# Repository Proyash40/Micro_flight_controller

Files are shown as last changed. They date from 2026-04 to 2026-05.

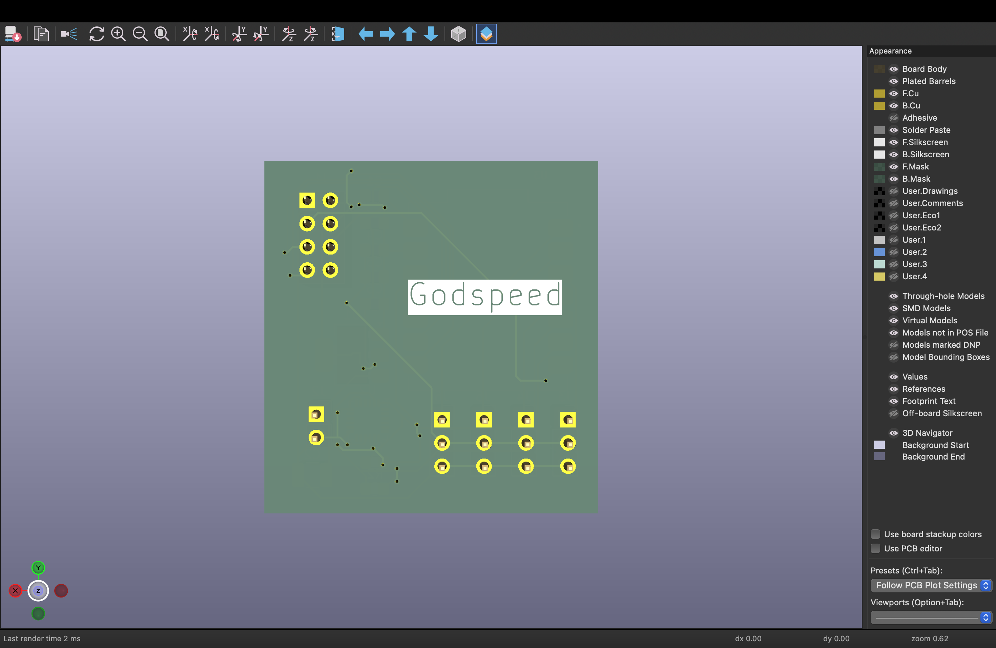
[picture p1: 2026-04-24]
IMAGES/silkscreen2_3d.png

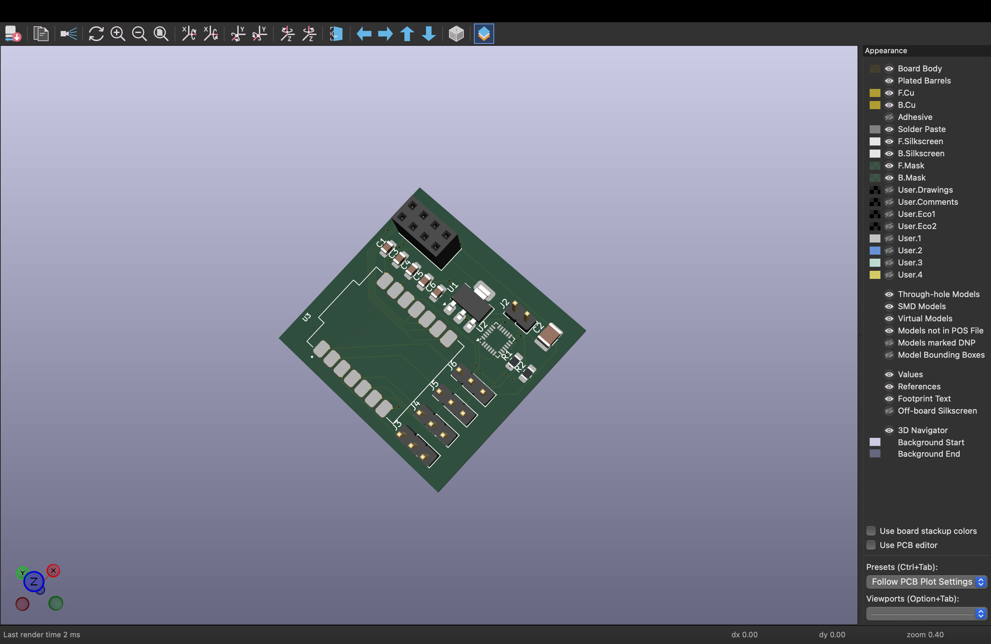
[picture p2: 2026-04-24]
IMAGES/3d_frontview.png

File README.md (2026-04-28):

### Micro flight controller 
Okay so I couldn't find a flight controller small enough or light enough for what I needed, so I just designed one from scratch lol.

It uses a seeed XIAO and a bunch of tiny SMD parts (0805 mostly). it actually works and flies pretty smooth but u have to be okay with soldering things the size of a grain of rice.

---

### What is this?

Basically a 4 channel RC flight computer. it takes throttle, aileron, elevator, and rudder from an nRF24 radio, runs it through some PID math at 100Hz, checks the gyro, and moves the servos so your plane doesn't instantly do a death flip.

### Stuff u need to build this (BOM)
---

| Name | Purpose | Quantity | Price (1 Unit) | Price Total(USD) | Links| 
| :-- | :-- | :-- | :-- | :-- | :-- |
| 4.7k smd resistor| I2C Pull-up for MPU6050  | 2 | $3.61 | $3.61 | [Link](https://robu.in/product/pro-range-resistor-assortment-kit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)|
| AMS1117 | Power Stability | 1 | $0.1 | $0.1 | [link](https://robu.in/product/ams1117-5-0-kexin-800ma-fixed-5v-positive-electrode-18v-sot-223-4-voltage-regulators-linear-low-drop-out-ldo-regulators-rohs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) |
| MPU6050 | 3 axis gyro + accelerometer | 1 | $2.55 | $2.55 | [link](https://quartzcomponents.com/products/mpu-6050-3-axis-gyro-accelerometer-ic-tdk-invensense-qfn-24-smd-package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) |
| Seeed studio XIAO ESP32 supermini C3 | The main brain | 1 | $9.56 | $9.56 | [Link](https://robu.in/product/seeed-studio-xiao-esp32s3-2-4ghz-wifi-ble-5-0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) |
| PCB print | Holding all the components together | 1 | $ 3 | $3 | [Link](https://cart.jlcpcb.com/quote)
| Capacitor 0.1uF (100nF) 0805| Decoupling for MPU6050 | 3 | -- | -- | I'd recomend buying it offline |
| Capacitor 2.2nF 0805 | MPU6050 Charge Pump | 1 |  -- | -- | I'd recomend buying it offline |
| Capacitor 10uF 0805 | AMS1117 Input Filter| 2 |  -- | -- | I'd recomend buying it offline |
| Capacitor 100uF 1210 | nRF24 Power Buffer* | 2 | -- | -- | I'd recomend buying it offline |

### IMPORTANT RANT ABOUT SOLDER

Do NOT use cheap 60/40 or 35/65 solder for this. The vibrations from the drone motors will crack your joints. buy actual 63/37 (Tin/Lead) Rosin Core 0.5mm wire. It solidifies instantly and doesn't get mushy. Soldron is fine. Just don't buy the cheap unbranded tubes.

### Software stuff

The code is in C++. don't use the normal arduino IDE for this, it sucks for complex stuff. Use VS Code + PlatformIO.

### Libraries u need:

RF24 (for the radio)

MPU6050_light (so much better than writing custom kalman filters)

PID_v1 (for the stabilization math)

---

Note: The loop is locked at 100Hz so the servos don't twitch themselves to death. The I2C is boosted to 400kHz so the gyro reads fast enough.

---

### How to fly 

1) Turn on radio.

2) Plug in battery.

3) DO NOT touch the plane for like 3 seconds while the MPU6050 calibrates.

4) Arm the throttle (push it up past 1050us).

5) Pray your PID tuning is right.

---

### Images

rough_idea

Screenshot 2026-04-28 at 12 12 12 PM

schematic

schematic1

pcb

silkscreen1

3d_frontview

silkscreen2_3d

---
If u haven't flown any rc before, I'd recomend to let someone experienced fly it first unless you want to destroy all your hard work on  the first flight.

---
(Disclaimer: if u copy my PID values and your plane nosedives into a tree, that's on u. tune it yourself for your airframe).

Have fun ✌️

### ~GODSPEED

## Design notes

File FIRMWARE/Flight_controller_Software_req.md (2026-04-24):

Flight Controller - Firmware Dependencies

## Development Environment
* **IDE:** VS Code with the PlatformIO extension (Highly recommended over the basic Arduino IDE for a project this complex).
* **Framework:** Arduino Core
* **Board Manager URL/Package:** * `Earle Philhower's arduino-pico` (If using the XIAO RP2040)
  * `Seeed nRF52 mbed-enabled Boards` (If using the XIAO nRF52840)

## Core Libraries (Install via Library Manager)

### 1. Radio Communication
* **Library:** `RF24` 
* **Author:** TMRh20
* **Purpose:** The absolute gold standard for driving the nRF24L01. It handles the SPI communication, packet payloads, and error checking.

### 2. Sensor Fusion (MPU6050)
* **Library:** `MPU6050_Light` 
* **Author:** Romain Fétick (rfetick)
* **Purpose:** This is the secret weapon for DIY drones. Instead of reading raw, noisy accelerometer data and writing your own Kalman filters, this library automatically calculates the clean Pitch, Roll, and Yaw angles fast enough for a flight controller. 

### 3. Flight Stabilization (The Math)
* **Library:** `PID_v1`
* **Author:** Brett Beauregard
* **Purpose:** You need a PID (Proportional, Integral, Derivative) loop for Pitch, Roll, and Yaw to keep the plane level. This library handles the complex calculus for you. You just feed it your current angle and your desired angle, and it outputs the correction needed.

### 4. Hardware Outputs
* **Library:** `Servo` (Built-in)
* **Purpose:** Generates the exact 50Hz PWM signals required to talk to the ESC (Throttle) and the 3 Servos (Aileron, Elevator, Rudder).

## The Core Software Architecture (The Loop)
Your `void loop()` must run as fast as possible (target >100Hz) in this exact order:
1. **Radio Rx:** Check if a new command packet arrived from the transmitter.
2. **Read IMU:** Get the current pitch/roll angle from the MPU6050.
3. **Compute PID:** Compare the pilot's command to the current angle and calculate the difference.
4. **Mixer:** Mix the PID outputs to figure out exactly how far to move each servo.
5. **Output:** `Servo.write()` the new values to the physical pins.

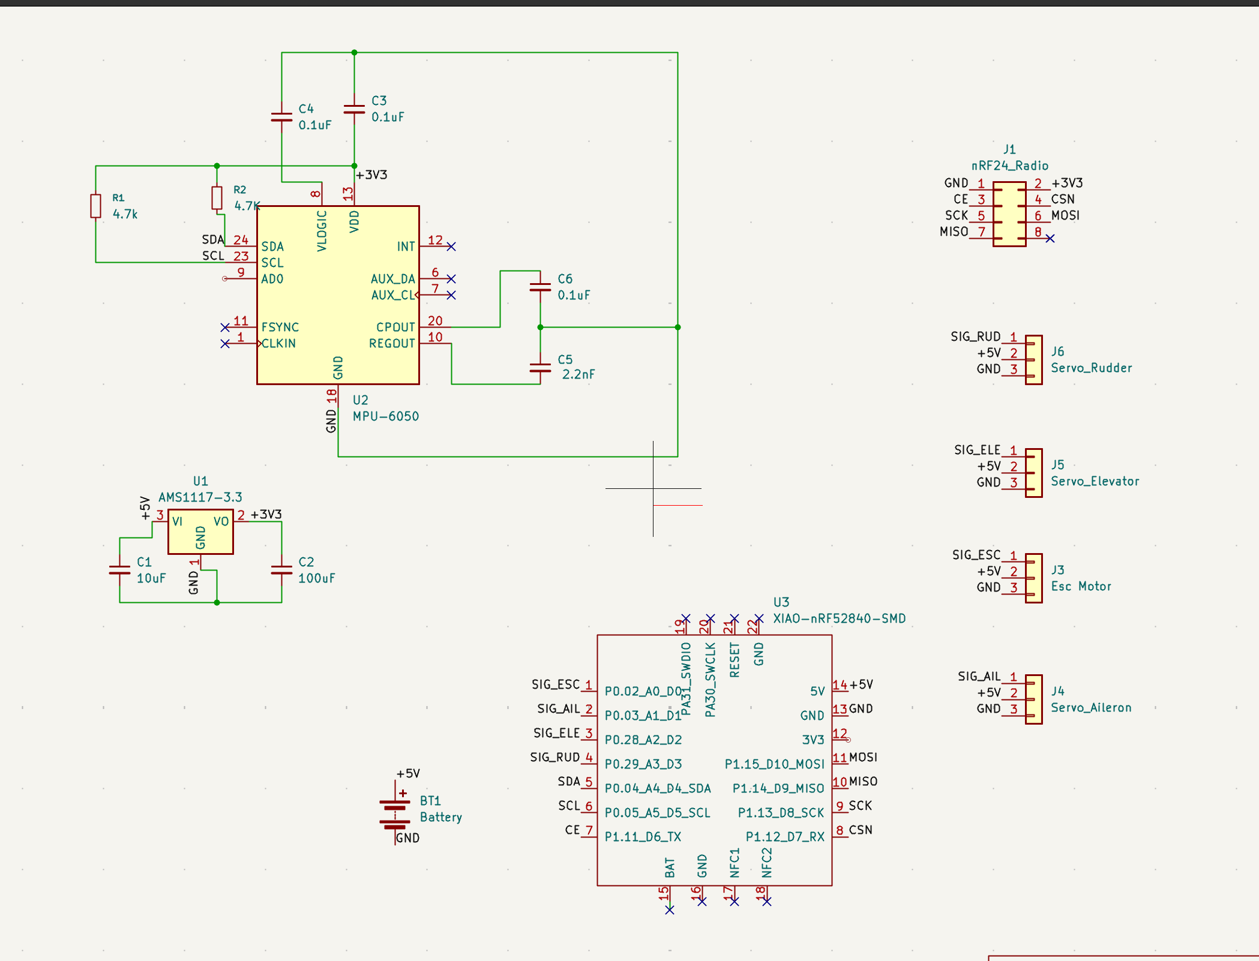
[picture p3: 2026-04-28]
IMAGES/schematic.png

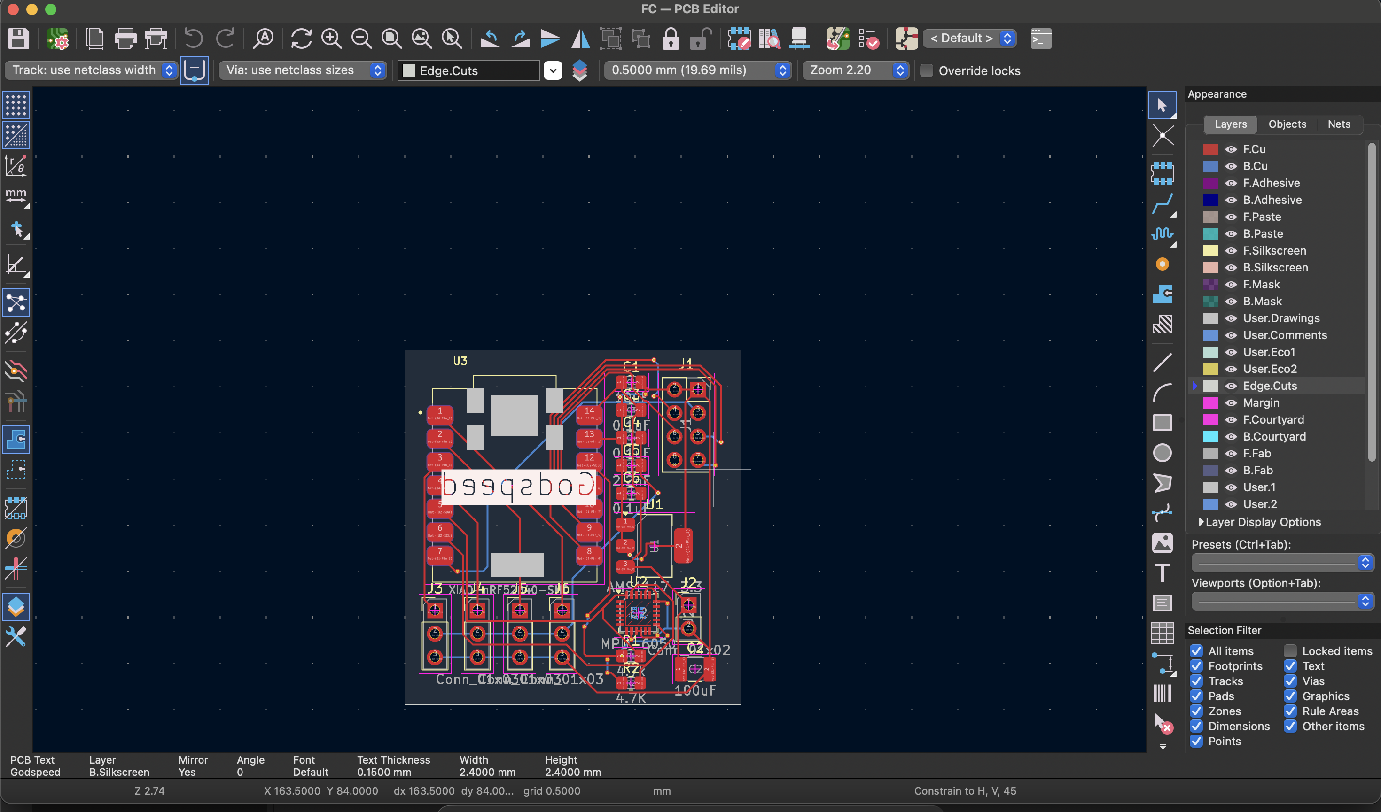
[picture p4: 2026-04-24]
IMAGES/silkscreen1.png

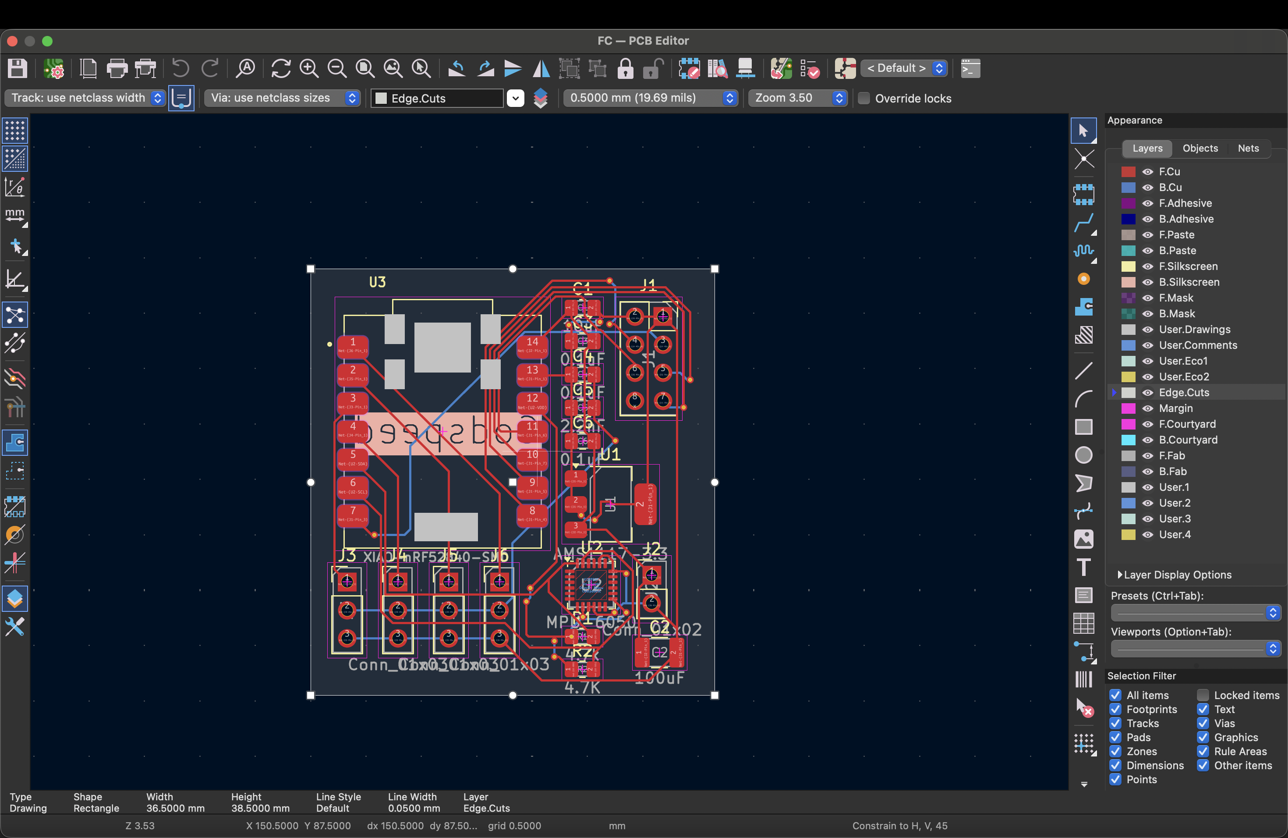
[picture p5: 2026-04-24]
IMAGES/pcb.png

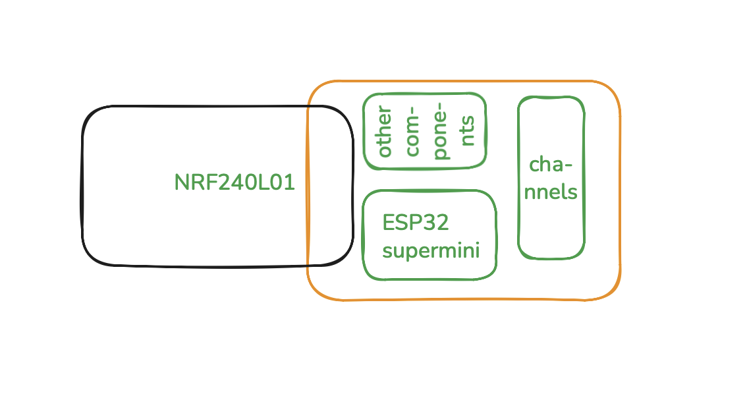
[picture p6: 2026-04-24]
IMAGES/rough_idea.png

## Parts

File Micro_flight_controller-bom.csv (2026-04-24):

Name | Purpose | Quantity | Total Cost (USD) | Link | Distributor
4.7k resistance | I2C Pull-ups for MPU6050 | 1 | 3.61 | https://robu.in/product/pro-range-resistor-assortment-kit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 | Robu.in
AMS1117 | power stability | 1 | 0.10 | https://robu.in/product/ams1117-5-0-kexin-800ma-fixed-5v-positive-electrode-18v-sot-223-4-voltage-regulators-linear-low-drop-out-ldo-regulators-rohs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 | Robu.in
MPU6050 | 3 axis Gyro+ accelerometer | 1 | 2.55 | https://quartzcomponents.com/products/mpu-6050-3-axis-gyro-accelerometer-ic-tdk-invensense-qfn-24-smd-package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 | Quartz components
Seeed studio ESP32 | The main brain | 1 | 9.56 | https://robu.in/product/seeed-studio-xiao-esp32s3-2-4ghz-wifi-ble-5-0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 | Robu.in

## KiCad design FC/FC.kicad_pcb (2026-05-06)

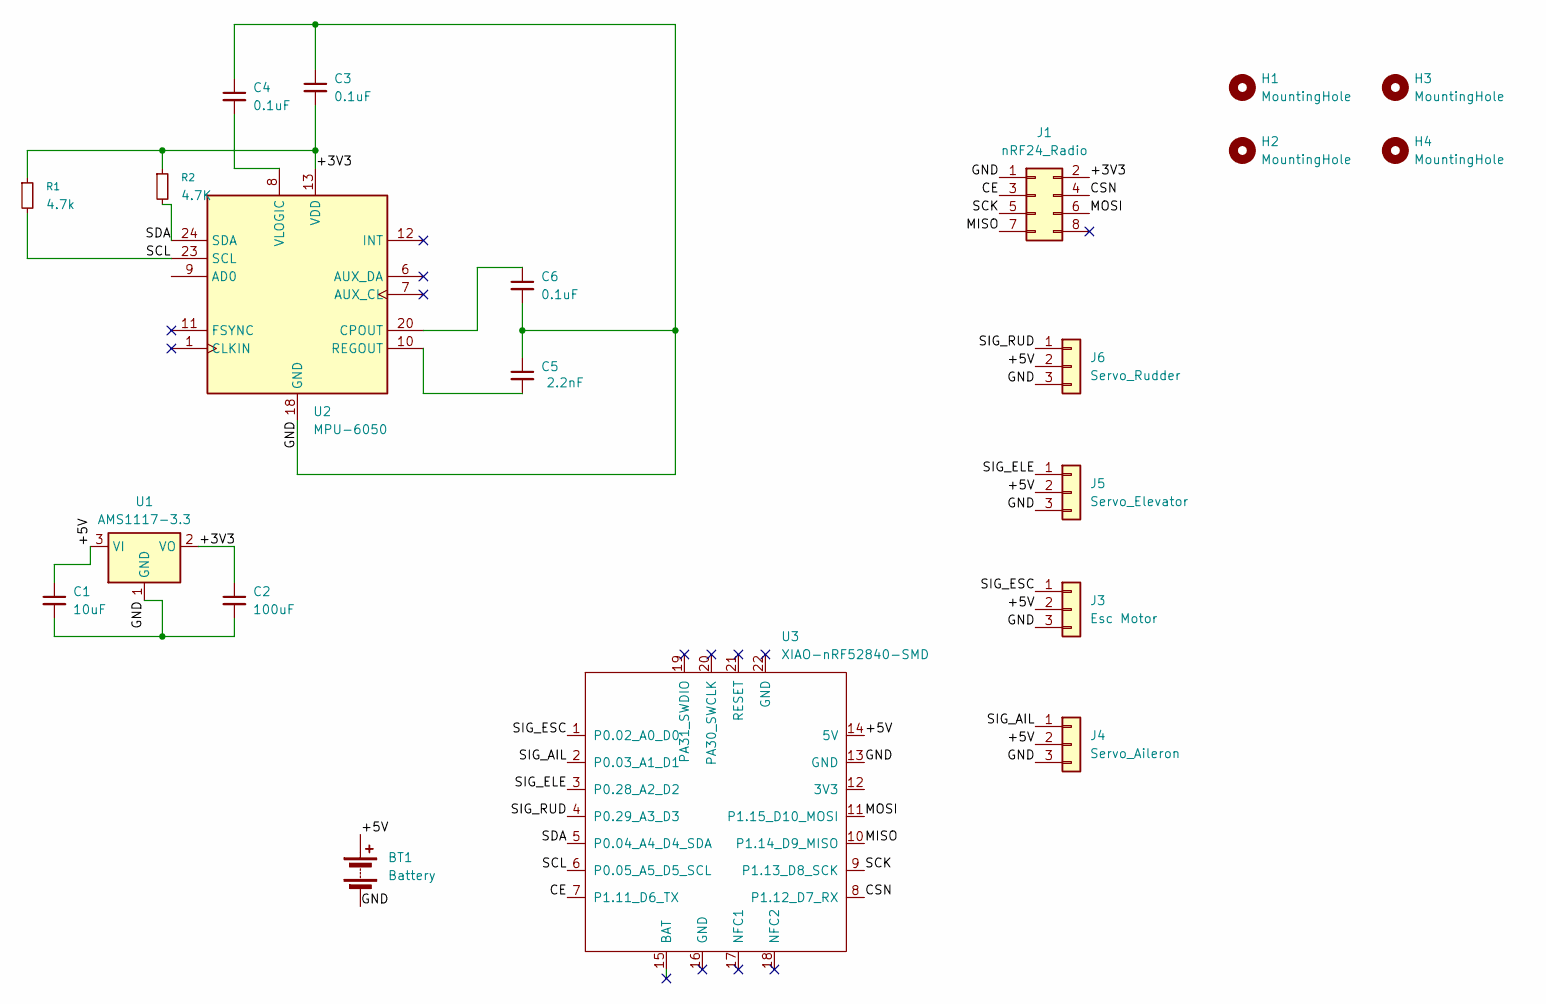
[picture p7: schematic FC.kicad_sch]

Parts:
BT1: Battery; MountingHole_2.2mm_M2
C1: 10uF; C_0805_2012Metric_Pad1.18x1.45mm_HandSolder
C2: 100uF; C_1210_3225Metric_Pad1.33x2.70mm_HandSolder
C3, C4, C6: 0.1uF; C_0805_2012Metric_Pad1.18x1.45mm_HandSolder
C5: 2.2nF; C_0805_2012Metric_Pad1.18x1.45mm_HandSolder
H1, H2, H3, H4: MountingHole; MountingHole_2.2mm_M2
J1: nRF24_Radio; PinSocket_2x04_P2.54mm_Vertical
J3: Esc Motor; PinHeader_1x03_P2.54mm_Vertical
J4: Servo_Aileron; PinHeader_1x03_P2.54mm_Vertical
J5: Servo_Elevator; PinHeader_1x03_P2.54mm_Vertical
J6: Servo_Rudder; PinHeader_1x03_P2.54mm_Vertical
R1: 4.7k; R_0805_2012Metric_Pad1.20x1.40mm_HandSolder
R2: 4.7K; R_0805_2012Metric_Pad1.20x1.40mm_HandSolder
U1: AMS1117-3.3; SOT-223-3_TabPin2
U2: MPU-6050; InvenSense_QFN-24_4x4mm_P0.5mm
U3: XIAO-nRF52840-SMD; MODULE_102010428

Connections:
/+3V3: C2.1, C3.2, J1.2, R1.1, R2.1, U1.2 (VO), U2.13 (VDD)
/+5V: BT1.1 (+), C1.1, J3.2, J4.2, J5.2, J6.2, U1.3 (VI), U3.14 (5V)
/<NO NET>: J5.1, U3.3 (P0.28_A2_D2)
/CE: J1.3, U3.7 (P1.11_D6_TX)
/CSN: J1.4, U3.8 (P1.12_D7_RX)
/GND: BT1.2 (-), C1.2, C2.2, C3.1, C4.1, C5.1, C6.2, J1.1, J3.3, J4.3, J5.3, J6.3, U1.1 (GND), U2.18 (GND), U3.13 (GND)
/MISO: J1.7, U3.10 (P1.14_D9_MISO)
/MOSI: J1.6, U3.11 (P1.15_D10_MOSI)
/SCK: J1.5, U3.9 (P1.13_D8_SCK)
/SCL: R1.2, U2.23 (SCL), U3.6 (P0.05_A5_D5_SCL)
/SDA: R2.2, U2.24 (SDA), U3.5 (P0.04_A4_D4_SDA)
/SIG_AIL: J4.1, U3.2 (P0.03_A1_D1)
/SIG_ESC: J3.1, U3.1 (P0.02_A0_D0)
/SIG_RUD: J6.1, U3.4 (P0.29_A3_D3)
unnamed: C6.1, U2.20 (CPOUT)
unnamed: C5.2, U2.10 (REGOUT)
unnamed: C4.2, U2.8 (VLOGIC)

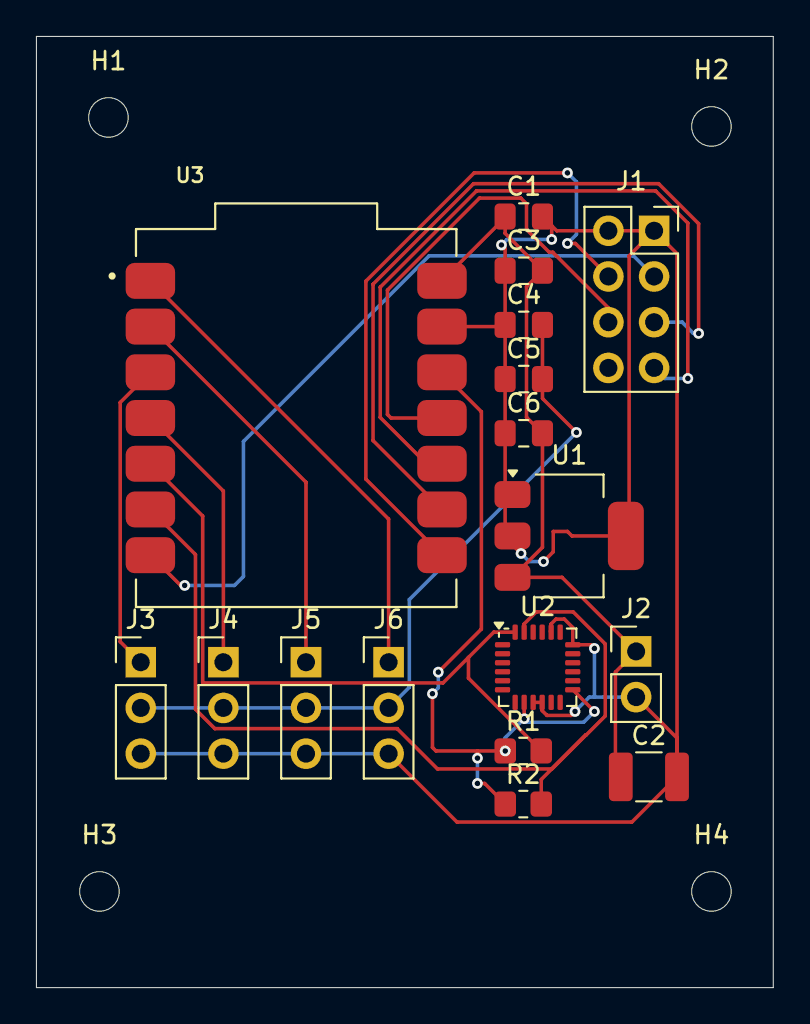
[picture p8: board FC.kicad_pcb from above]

Board: 2 copper layers, 40.9 x 52.8 mm, 21 parts (0 on the bottom side), 17 nets.

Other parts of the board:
J2: Conn_01x02; PinHeader_1x02_P2.54mm_Vertical

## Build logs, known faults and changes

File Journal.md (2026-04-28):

### Journal :-

| Title | Micro Flight Controller |
| :-- | :---|
|Author | Proyash Kumar Sarkar (Godspeed)|
|Project Tire | 3|

### Components searching, basic design

This was my first time designing a cutom flight controller. Prior to this i had flown rc planes nd had experience with transmitter nd receiver making, so with a certain motivation by my frnd, i started working on this project.

At the begining i had to know about the componets of the flight controller, the sensors or function it does, then chose the right material and the smaller the better. We all know how hard its to make rc plane fly with heavy components.

So the first challenge was to find the componets small enough and fits the budget. First i was seacrhing for [ELRS](https://robu.in/product/radiomaster-tx16s-mkii-hall-v4-0-elrs-radio-controller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) modules then saw the price nd nearly pulled my heart out. So i went with the standard NRF240L01+(PA+LNA) module, it gives a range for about 700-1km, which is fairly good enough for a beginner project. {Cutting cost does comes with some drawbacks🥲}

Howsoever, after that, chossing the main brain, yea it was hecktic. Cz I myself prefer design PCB with KiCAD, now it doesn't have the footprint nor the library nor the symbol for Seeed studio Xiao ESP32 supermini. So i was thinking what the brain i might use. I called one of my friend nd he advised me to see this [video](https://www.youtube.com/watch?v=W9cLnIjvybo) by [PlumPot](https://www.youtube.com/@PlumPot). Then learnt how to insert or import whatever, to KiCAD and use it, so i went with the ESP32. (I used nothing else due to its tiny size and processing speed)

At the end i chose the MPU6050 module, it has 3 axis gyro and additionally accelerometer.

So finnally this was the basic design. I just tried to make the Flight Controller as small as possible.

---

rough_idea

---

Now lets see, how small I can make the PCB✌🏻

---
### The circuit design

Screenshot 2026-04-28 at 12 12 12 PM

This was my circuit diagram, I know its very hard to understand, so I'd recommned to look at the schematic which I'd make later on. And also I've not checked the whole diagram precisely, there is some issues with it which i ddecided to fix in the schematic.

---

### Schematic and PCB design

This morning, as soon as i woke up started gathering stuffs in KiCAD. But as i had mentioned in my last journal, it was pretty difficult to find the parts by their names. So I took some help for gemini and also google(not gonna lie😅)

So, after i found all the componenets and their libraries, i started making the schematic. For god's sake, it was very very difficult, i spent most of the time thinking, where to connect, nd with so many components. 😭

Though after a lot of struggle i managed to complete the schematic. Plot twist, as soon as I ran ERC, it gave a bunch of errors and warnings. It was my time to start crying. I slammed my laptop off, and went to bed with spotify at the full volume of my music system. Nd my mom came with her slippers in hand.😂

So I put on my headphones nd slept. after about an hour or so I woke up did some Maths for upcoming exams.(Yea ive not included this time in the session time). Then with a fresh mind i started making the schematic again and boom, i succesfully made the schematic.

---
schematic

---
schematic1

I later cleanedup the schematic for a better understanding. And note that I've forgotten to add the "no connection mark" on the ESP32 3V3 pin, it wont create any blunder but while running ERC, it might show as unconnected port, thats all.

:) 
---

Then assigned the footprints, I downloaded the footprint for this specific ESP32 from [here](https://www.snapeda.com/parts/102010428/Seeed%20Technology%20Co.%2C%20Ltd/view-part/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) and added to my library. Though it was pretty easy, but i forgot to save the footprint at first, nd was really screaming when i switched to PCB mode, as i couldn't see any of the components. Then i again went back and saved the footprints. Joined the wires again and prepared my mini PCB which is almost as small as a 4*4 cm square.

---

pcb

---

### Searching on Web for availability of the components

So finally after web screapping a lot, i found the materials i required and additonally keeping in mind the budget. So these given below are my whole listt of components. Hopefully they work all fine nd i myself don't make any mistake😅

---
robu_bill

quartz_components_bill

jlc_pcb_bill

---

### Project under [Stasis](https://stasis.hackclub.com/dashboard/projects/cmobnjizc019h01mn31wxweli)

### ~GODSPEED

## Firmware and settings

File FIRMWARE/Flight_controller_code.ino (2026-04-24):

#include <Wire.h>
#include <Servo.h>
#include <RF24.h>
#include <MPU6050_light.h>
#include <PID_v1.h>

RF24 radio(6, 7);
const byte address[6] = "00001";

MPU6050 mpu(Wire);

Servo esc;
Servo aileron;
Servo elevator;
Servo rudder;

struct RadioPacket {
  int throttle;
  int pitch;
  int roll;
  int yaw;
  bool arm;
};

RadioPacket data;

double pitchInput, pitchOutput, pitchSetpoint;
double rollInput, rollOutput, rollSetpoint;

double kp = 2.0, ki = 0.5, kd = 1.0;

PID pitchPID(&pitchInput, &pitchOutput, &pitchSetpoint, kp, ki, kd, DIRECT);
PID rollPID(&rollInput, &rollOutput, &rollSetpoint, kp, ki, kd, DIRECT);

unsigned long lastRecvTime = 0;
unsigned long loopTimer = 0;
bool isArmed = false;

void setup() {
  Wire.setClock(400000);
  Wire.begin();
  
  mpu.begin();
  mpu.calcOffsets(true, true);
  
  radio.begin();
  radio.openReadingPipe(0, address);
  radio.setPALevel(RF24_PA_MAX);
  radio.setDataRate(RF24_2MBPS);
  radio.startListening();
  
  esc.attach(0, 1000, 2000);
  aileron.attach(1);
  elevator.attach(2);
  rudder.attach(3);
  
  esc.writeMicroseconds(1000);
  
  pitchPID.SetMode(AUTOMATIC);
  pitchPID.SetOutputLimits(-400, 400); 
  pitchPID.SetSampleTime(10);
  
  rollPID.SetMode(AUTOMATIC);
  rollPID.SetOutputLimits(-400, 400);
  rollPID.SetSampleTime(10);

  data.throttle = 1000;
  data.pitch = 512;
  data.roll = 512;
  data.yaw = 512;
  data.arm = false;

  loopTimer = micros();
}

void loop() {
  mpu.update(); 

  if (radio.available()) {
    radio.read(&data, sizeof(RadioPacket));
    lastRecvTime = millis();
  }
  
  if (millis() - lastRecvTime > 500) {
    data.throttle = 1000;
    data.pitch = 512;
    data.roll = 512;
    data.yaw = 512;
    data.arm = false;
  }

  if (data.arm && data.throttle < 1050) {
    isArmed = true;
  } else if (!data.arm) {
    isArmed = false;
  }
  
  if (micros() - loopTimer >= 10000) {
    loopTimer = micros();
    
    pitchInput = mpu.getAngleY();
    rollInput = mpu.getAngleX();
    
    pitchSetpoint = map(data.pitch, 0, 1023, -30, 30);
    rollSetpoint = map(data.roll, 0, 1023, -30, 30);

    if (!isArmed || data.throttle < 1050) {
      pitchPID.SetMode(MANUAL);
      rollPID.SetMode(MANUAL);
      pitchOutput = 0;
      rollOutput = 0;
      pitchPID.SetMode(AUTOMATIC);
      rollPID.SetMode(AUTOMATIC);
    } else {
      pitchPID.Compute();
      rollPID.Compute();
    }
    
    int aileronVal = 1500 + rollOutput;
    int elevatorVal = 1500 - pitchOutput;
    int rudderVal = map(data.yaw, 0, 1023, 1100, 1900); 
    
    if (isArmed) {
      esc.writeMicroseconds(data.throttle);
    } else {
      esc.writeMicroseconds(1000);
    }
    
    aileron.writeMicroseconds(constrain(aileronVal, 1100, 1900));
    elevator.writeMicroseconds(constrain(elevatorVal, 1100, 1900));
    rudder.writeMicroseconds(constrain(rudderVal, 1100, 1900));
  }
}
